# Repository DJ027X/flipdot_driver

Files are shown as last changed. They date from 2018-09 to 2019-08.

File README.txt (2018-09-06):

######################
A word about the license
######################
In this repo, you'll find the EDA design files for my RISC-V based flipdot display driver.
In the interest of preventing an entity from profiting off of my work or its derivitives without my permission, everything in this repo is released under the Creative Commons license BY-NC-SA.
Feel free to modify and redistribute my work (with attribution to me, and under the same BY-NC-SA license), just don't use the work for profit.
Please contact me if you would like to request exemption from the terms of the license.

######################
Project progress
######################
This project is INCOMPLETE and IN-PROGRESS.
At the moment, only the schematic exists; no layout design yet.
The schematic is very near completion, and I'm currently working on finishing touches, and reviewing the design.

######################
Design details/notes
######################
This project is being designed with the open-source KiCAD toolchain. I'm tending toward openness with this project, but my design does use an FT2232D, and my license isn't truly FOSS compliant. More FOSS friendly versions may come up in the future.
My flipdot display driver is intended for use with a Luminator MAX 3000 flipdot display.
My board will mount onto the back of the flipdot display, and connect to it via a board-to-board connector (samtec part SSQ-132-01-G-Q at the moment).
Each dot on the Luminator MAX 3000 is matrixed in such a way that lends itself to be driven by what is essentially an H-bridge. (diodes in the display circuitry complicate things a tad, which is why it's not exactly an H-bridge driver, but pretty close)
My driver uses power MOSFETs arranged in an H-bridge-like topology to drive current in short (on the order of millisecond) pulses in one direction or another through the coil of each dot to flip it on (bright side visable) or off (black side visible), depending on the cirection of the current
There is 1/2 of this H-bridge-like circuit (quarter bridge?) driving each row and column on the display, effectively allowing the driver to multiplex the dots.
The quarter-bridge driver circuitry is controlled by data stored in 2 (extendable) shift registers, one for the rows and one for the columns.
Pulsing an output enable signal on the shift registers drives the selected quarter-bridge circuits (based on the output from the shift register) for the duration of the pulse.
If one wishes to extend their display with yet another (actually, an arbitrary number of) Luminator MAX 3000 board, I've added a connector that will be used (when I get around to designing the second board) to extend the shift registers to the additional board, which will house it's own section of the shift register and dedicated quarter-bridge driver circuitry.
The brain of the operation is the FE310-G000, a VERY new RISC-V based microcontroller released by SiFive.
Along with the uC are the typical auxilary chips: memory and serial to UART/JTAG to program the uC.
The Luminator MAX 3000 also has 1 LED per dot. They are all connected to the same power pins, so they're either all on, or all off.
I intend to control the brightness with PWM.
Under normal use, the board will be supplied with 12V from a power brick. From there, several buck converters will provide the voltages for the shift registers, memory, uC, etc.
There will also be a voltage negater (generating -12V), to provide a potential of 24V for the LEDs.
I'm currently working full time, so progress on this relatively large hobby project has been slow, but I'll have a physical board eventually! (Aiming for 3 months from now (12/27/2018))

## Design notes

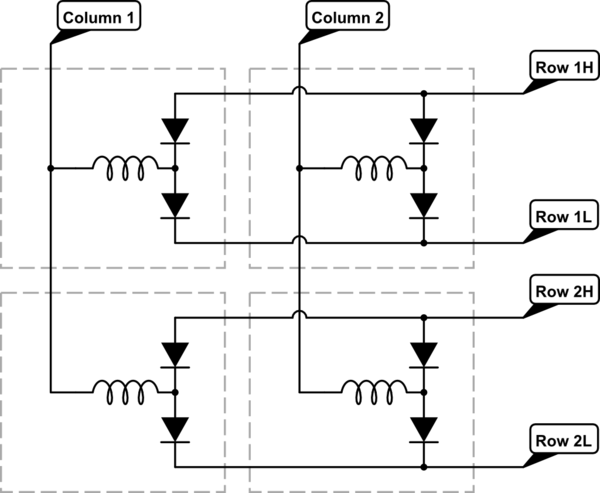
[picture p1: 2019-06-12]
cell_circuit.png

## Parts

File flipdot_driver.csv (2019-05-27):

Reference | Quantity | Value | Footprint | Datasheet | Rating | Capacitance | NP | Resistance
C1 C10 C18 C21 C24 C27 C33 C34 C35 C37 C38 C4 C43 C44 C45 C47 C48 C51 C55 C56 C58 C65 C67 C7 C71 C78 C80 C82 | 28 | CL10B104KO8NNNC | Capacitor_SMD:C_0603_1608Metric | datasheets/CL10B104KO8NNNC.pdf | 16V | 0.1uF
C13 | 1 | NP_470uF
C14 C15 | 2 | ‎ESK476M035AC3AA‎ |  | datasheets/‎KEM_A4004_ESK.pdf | 35V | 47uF
C11 C19 C2 C22 C25 C28 C36 C46 C5 C52 C57 C59 C66 C68 C70 C74 C79 C8 C81 C83 | 20 | CL10B105KA8NNNC | Capacitor_SMD:C_0603_1608Metric | datasheets/CL10B105KA8NNNC.pdf | 25V | 1uF
C12 C20 C23 C26 C29 C3 C39 C49 C53 C6 C69 C84 C9 | 13 | NP_C_0603 | Capacitor_SMD:C_0603_1608Metric |  |  |  | NP
C16 C17 C30 C31 C32 | 5 | ‎CL21A475KLCLQNC‎ | Capacitor_SMD:C_0805_2012Metric | datasheets/‎CL21A475KLCLQNC‎.pdf | 35V | 4.7uF
C40 C41 | 2 | EEE-1VA220SP |  | datasheets/EEE-1VA220SP.pdf | 35V | 22uF
C42 | 1 | 885012206087 | Capacitor_SMD:C_0603_1608Metric | datasheets/885012206087.pdf | 50V | 4.7nF
C50 | 1 | ‎CL10B153KB8SFNC‎ | Capacitor_SMD:C_0603_1608Metric | datasheets/‎CL10B153KB8SFNC‎.pdf | 50V | 15nF
C54 | 1 | 33nF | Capacitor_SMD:C_0603_1608Metric
C60 C62 C75 C77 | 4 | CL21A226MOCLRNC | Capacitor_SMD:C_0805_2012Metric | datasheets/CL21A226MOCLRNC.pdf | 16V | 22uF
C61 C76 | 2 | ‎C0603C470J1GACTU‎ | Capacitor_SMD:C_0603_1608Metric | datasheets/‎C0603C470J1GACTU‎.pdf | 100V | 47pF
C63 C64 C72 C73 | 4 | TMK042CG120JD-W‎ | Capacitor_SMD:C_01005_0402Metric | datasheets/TMK042CG120JD-W‎.pdf | 25V | 12pF
D1 D10 D11 D12 D13 D14 D15 D16 D17 D18 D19 D2 D20 D21 D22 D23 D24 D25 D26 D27 D28 D29 D3 D30 D31 D32 D4 D5 D6 D7 D8 D9 | 32 | MMBZ5243BLT1G |  |  | 13V
D33 D36 | 2 | DST2080S
D34 | 1 | SMAJ12A | Footprint
D37 | 1 | SMF5.0A | Footprint
D38 D39 | 2 | NP_UCLAMP2501T.TCT | Footprint
D40 | 1 | UCLAMP2501T.TCT | Footprint
D41 | 1 | RSB6.8F2T106
D35 D42 D43 D44 D45 D46 D47 | 7 | LED
J1 | 1 | 10x2_1&3_loaded_2.5mm_0.1in_female_header
J2 | 1 | Barrel_Jack | Connectors:BARREL_JACK
J3 | 1 | Screw_Terminal_01x04
J4 J6 | 2 | Conn_01x03_Male |  | ~
J5 | 1 | Conn_01x08_Male
J7 | 1 | USB-C_Connector
J8 | 1 | NP_Conn_01x06_Male
L1 L3 | 2 | FBMH4532HM681-T
L2 | 1 | 12uH
L4 | 1 | 6.5uH
L5 | 1 | 3.3uH
Q21 Q22 Q23 Q24 Q25 Q26 Q27 Q28 Q29 Q30 Q31 Q32 Q33 Q34 Q35 Q36 Q37 Q38 Q39 Q40 Q61 Q62 Q63 Q64 Q65 Q66 Q67 Q68 Q69 Q70 Q71 Q72 Q73 Q74 Q75 Q76 Q77 Q78 Q79 Q80 Q85 Q86 Q87 Q88 Q90 Q91 Q92 Q93 Q94 Q95 Q96 Q97 | 52 | SSM3K35AMFV |  | datasheets/SSM3K35AMFV.pdf
Q1 Q10 Q11 Q12 Q13 Q14 Q15 Q16 Q17 Q18 Q19 Q2 Q20 Q3 Q4 Q41 Q42 Q43 Q44 Q45 Q46 Q47 Q48 Q49 Q5 Q50 Q51 Q52 Q53 Q54 Q55 Q56 Q57 Q58 Q59 Q6 Q60 Q7 Q8 Q81 Q82 Q83 Q84 Q9 | 44 | DMG6602 | Package_TO_SOT_SMD:TSOT-23-6
Q89 | 1 | DMG6602 | TSOT-23-6
R155 | 1 | 300k | Resistors_SMD:R_0603_HandSoldering
R157 | 1 | 16.2k | Resistors_SMD:R_0603_HandSoldering
R159 | 1 | 200 | Resistors_SMD:R_0603_HandSoldering
R160 | 1 | 143k | Resistors_SMD:R_0603_HandSoldering
R165 R167 | 2 | 47 | Resistors_SMD:R_0603_HandSoldering
R134 R136 R140 R141 R143 R144 R148 R154 R166 R168 R178 R184 R185 R193 R195 R196 R197 | 17 | NP_R_0603 | Resistor_SMD:R_0603_1608Metric |  |  |  |  | NP
R171 | 1 | 1.5k | Resistors_SMD:R_0603_HandSoldering
R173 | 1 | 59k | Resistors_SMD:R_0603_HandSoldering
R172 R175 | 2 | 13k | Resistors_SMD:R_0603_HandSoldering
R169 R177 R181 | 3 | RC0603FR-0747KL | Resistor_SMD:R_0603_1608Metric | datasheets/‎SEI-RMCF_RMCP.pdf |  |  |  | 47k
R156 R164 R179 R192 R194 | 5 | RC0603JR-070RL | Resistor_SMD:R_0603_1608Metric | datasheets/‎PYu-RC_Group_51_RoHS_L_9.pdf |  |  |  | 0
R170 R180 | 2 | 40.2k | Resistors_SMD:R_0603_HandSoldering
R182 | 1 | 100k | Resistors_SMD:R_0603_HandSoldering
R183 | 1 | 32.4k | Resistors_SMD:R_0603_HandSoldering
R163 R186 R187 R188 R189 R190 R191 | 7 | ‎RMCF0603FT470R‎ | Resistor_SMD:R_0603_1608Metric | datasheets/SEI-RMCF_RMCP.pdf |  |  |  | 470
R1 R10 R100 R101 R102 R103 R104 R105 R106 R107 R108 R109 R11 R110 R111 R112 R113 R114 R115 R116 R117 R118 R119 R12 R120 R121 R122 R123 R124 R125 R126 R127 R128 R129 R13 R130 R131 R132 R133 R135 R137 R138 R139 R14 R142 R145 R146 R147 R149 R15 R150 R151 R152 R153 R158 R16 R161 R162 R17 R174 R176 R18 R19 R198 R199 R2 R20 R200 R201 R202 R203 R21 R22 R23 R24 R25 R26 R27 R28 R29 R3 R30 R31 R32 R33 R34 R35 R36 R37 R38 R39 R4 R40 R41 R42 R43 R44 R45 R46 R47 R48 R49 R5 R50 R51 R52 R53 R54 R55 R56 R57 R58 R59 R6 R60 R61 R62 R63 R64 R65 R66 R67 R68 R69 R7 R70 R71 R72 R73 R74 R75 R76 R77 R78 R79 R8 R80 R81 R82 R83 R84 R85 R86 R87 R88 R89 R9 R90 R91 R92 R93 R94 R95 R96 R97 R98 R99 | 157 | CRG0603F4K7 | Resistor_SMD:R_0603_1608Metric | datasheets/PYu-RC_Group_51_RoHS_L_9.pdf |  |  |  | 4.7k
SW1 | 1 | NP_TACTILE_SWITCH | CUSTOM:TACTILE_SWITCH
SW2 | 1 | TACTILE_SWITCH | CUSTOM:TACTILE_SWITCH
TP1 TP10 TP11 TP12 TP13 TP14 TP15 TP16 TP17 TP18 TP19 TP20 TP21 TP22 TP23 TP24 TP25 TP26 TP27 TP28 TP29 TP3 TP30 TP31 TP32 TP33 TP34 TP35 TP36 TP37 TP38 TP4 TP40 TP42 TP5 TP6 TP7 TP8 TP9 | 39 | TestPoint |  | ~
TP2 TP39 TP41 | 3 | TEST
U1 U10 U11 U14 U19 U2 U21 U3 U4 U5 U6 | 11 | 74HC595
U12 | 1 | TPS61175
U13 | 1 | FE310-G000
U16 | 1 | FT2232D | Housings_QFP:LQFP-48_7x7mm_Pitch0.5mm
U17 | 1 | IS25LP128-JBLE | Housings_SOIC:SOIC-8_3.9x4.9mm_Pitch1.27mm
U15 U18 | 2 | AP65111A
U20 U22 U7 U8 U9 | 5 | CM1293A-04SO |  | datasheets/CM1293A-04SO-D.PDF
Y1 | 1 | 16MHz
Y2 | 1 | 6MHz

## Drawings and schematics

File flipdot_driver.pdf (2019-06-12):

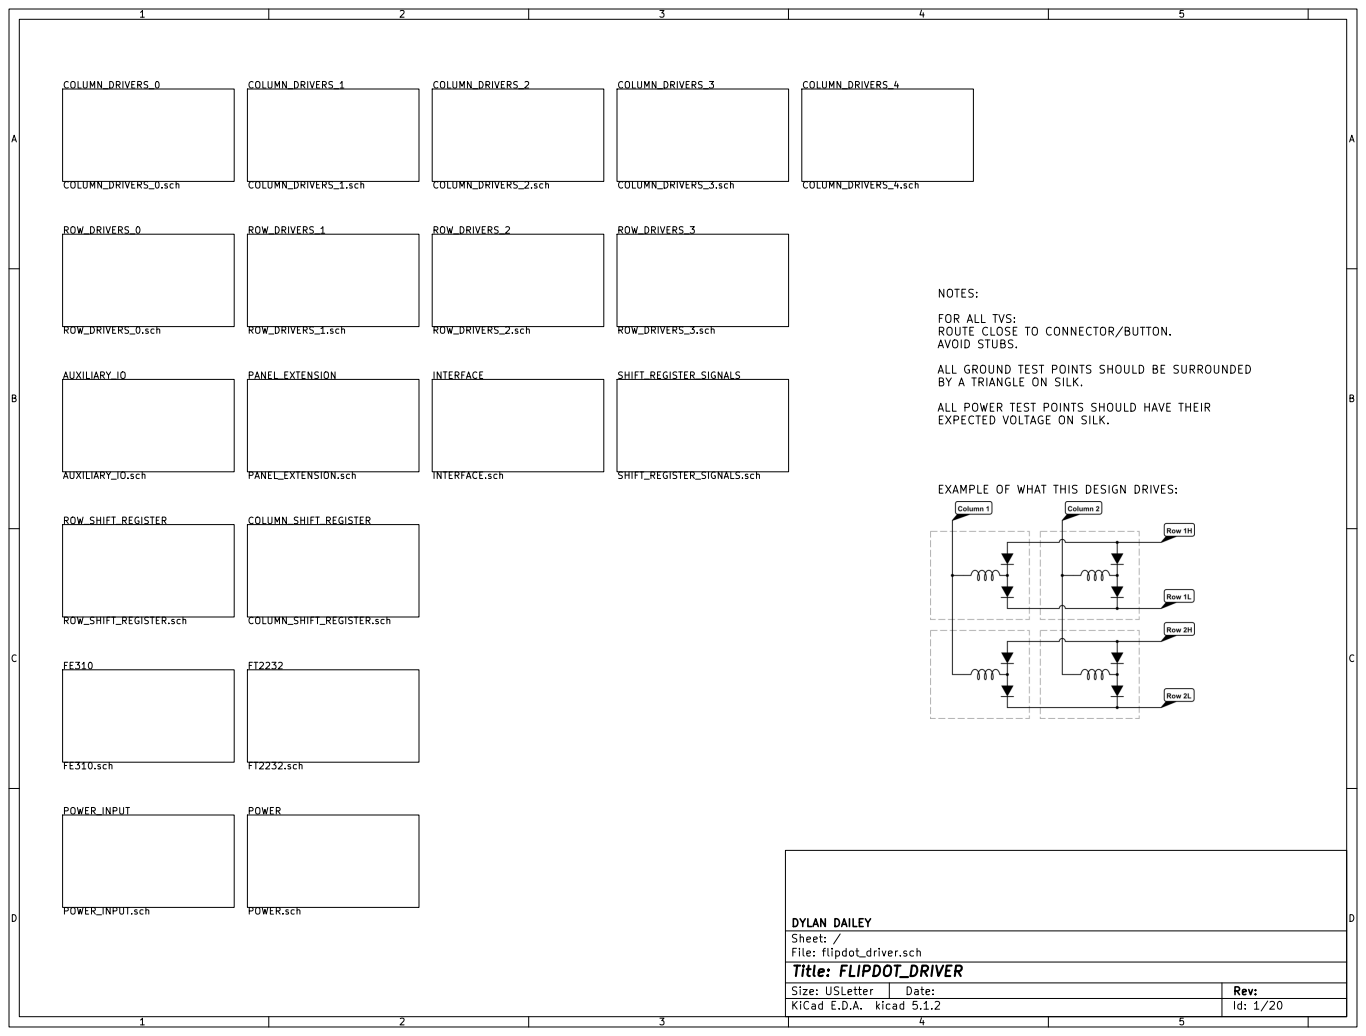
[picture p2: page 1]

FOR ALL TVS:
ROUTE CLOSE TO CONNECTOR/BUTTON.
AVOID STUBS.

ALL GROUND TEST POINTS SHOULD BE SURROUNDED
BY A TRIANGLE ON SILK.

ALL POWER TEST POINTS SHOULD HAVE THEIR
EXPECTED VOLTAGE ON SILK.

EXAMPLE OF WHAT THIS DESIGN DRIVES:

File: flipdot_driver.sch Sheet: / DYLAN DAILEY

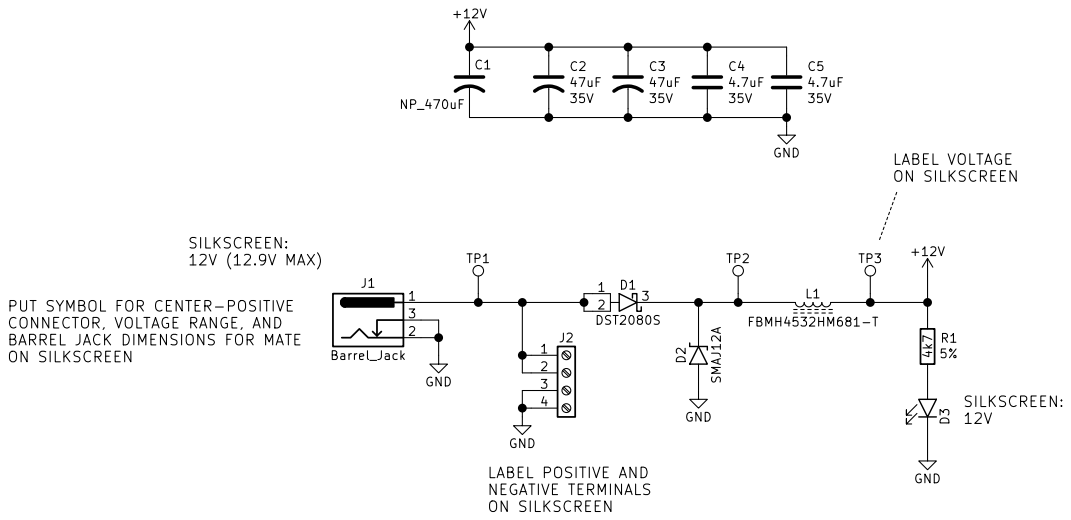
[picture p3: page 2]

J1 Barrel_Jack PUT SYMBOL FOR CENTER-POSITIVE

CONNECTOR, VOLTAGE RANGE, AND
BARREL JACK DIMENSIONS FOR MATE
ON SILKSCREEN

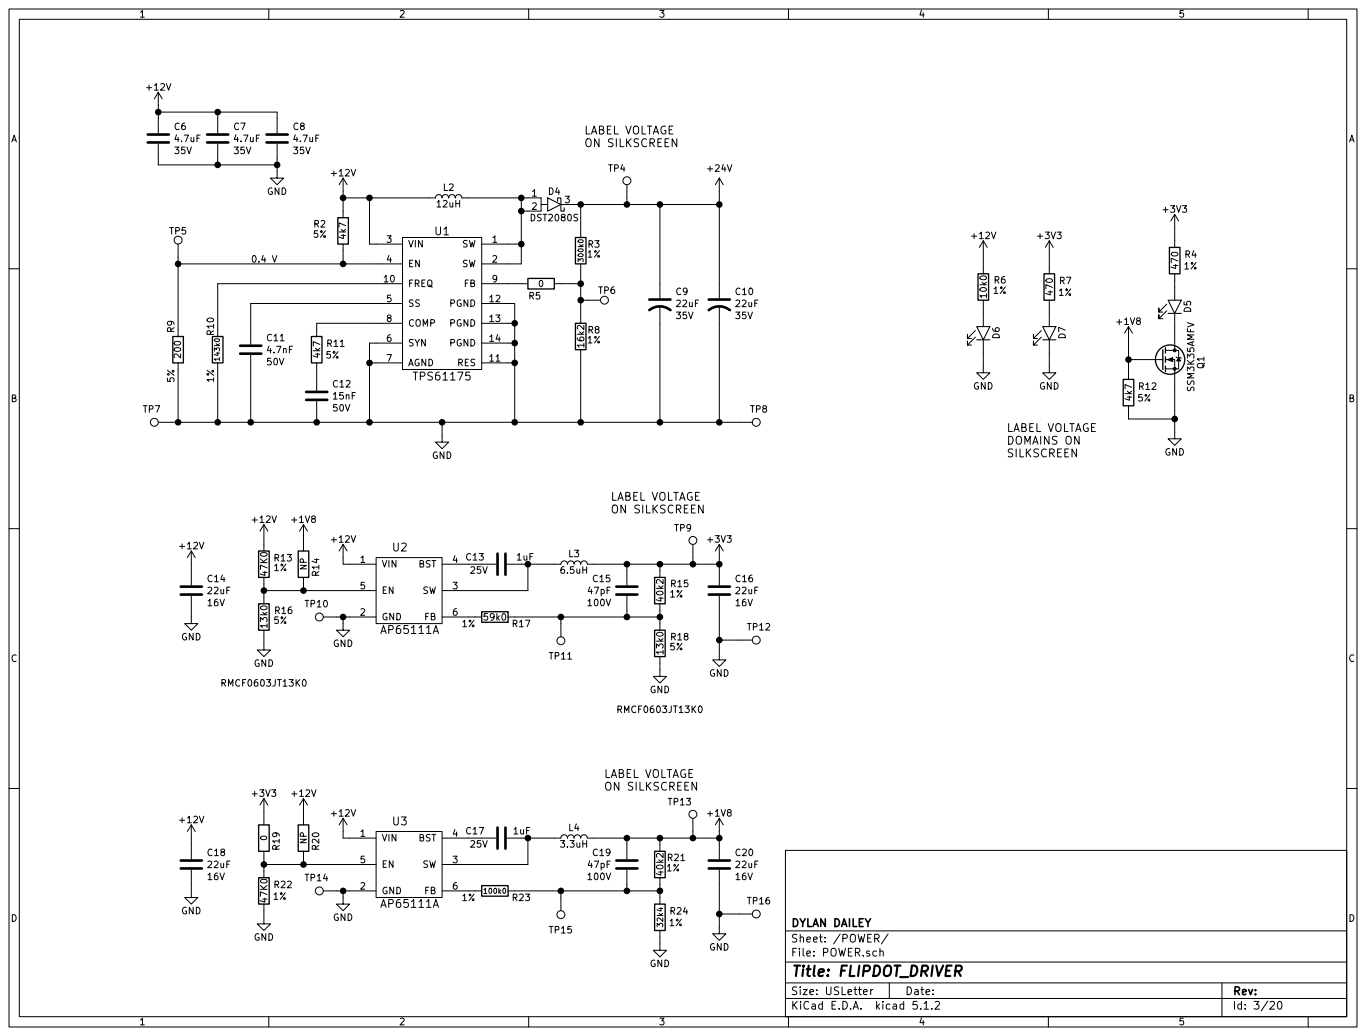
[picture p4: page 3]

File: POWER.sch Sheet: /POWER/ DYLAN DAILEY

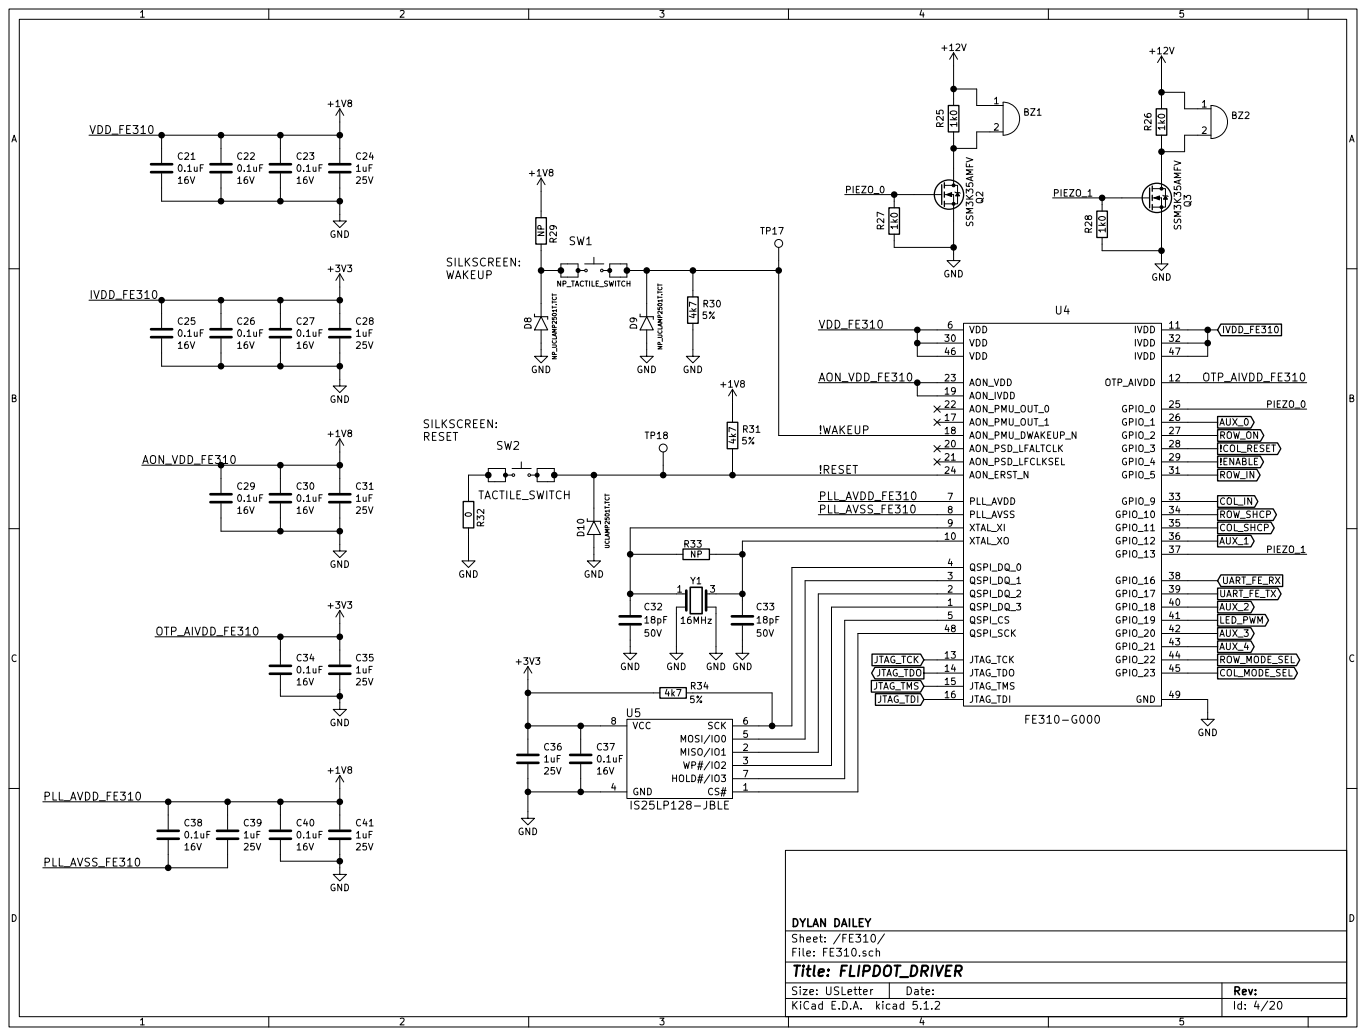
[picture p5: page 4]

File: FE310.sch Sheet: /FE310/ DYLAN DAILEY

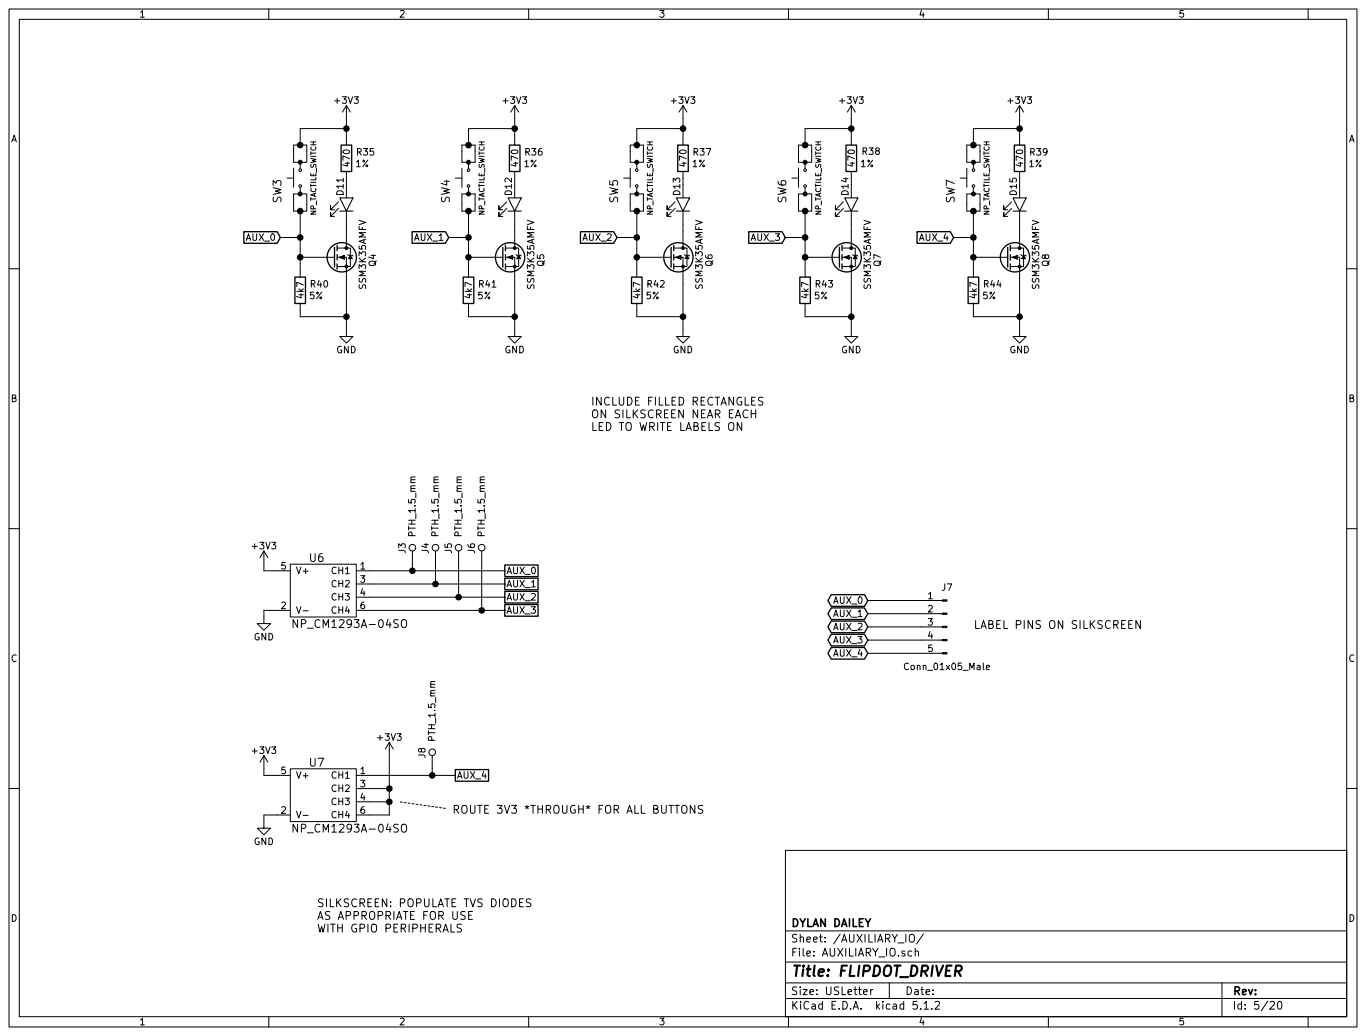
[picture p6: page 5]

INCLUDE FILLED RECTANGLES
ON SILKSCREEN NEAR EACH
LED TO WRITE LABELS ON

LABEL PINS ON SILKSCREEN J3 PTH_1.5_mm J4 PTH_1.5_mm J5 PTH_1.5_mm J6 PTH_1.5_mm

ROUTE 3V3 *THROUGH* FOR ALL BUTTONS

Sheet: /AUXILIARY_IO/ DYLAN DAILEY SILKSCREEN: POPULATE TVS DIODES
AS APPROPRIATE FOR USE
WITH GPIO PERIPHERALS

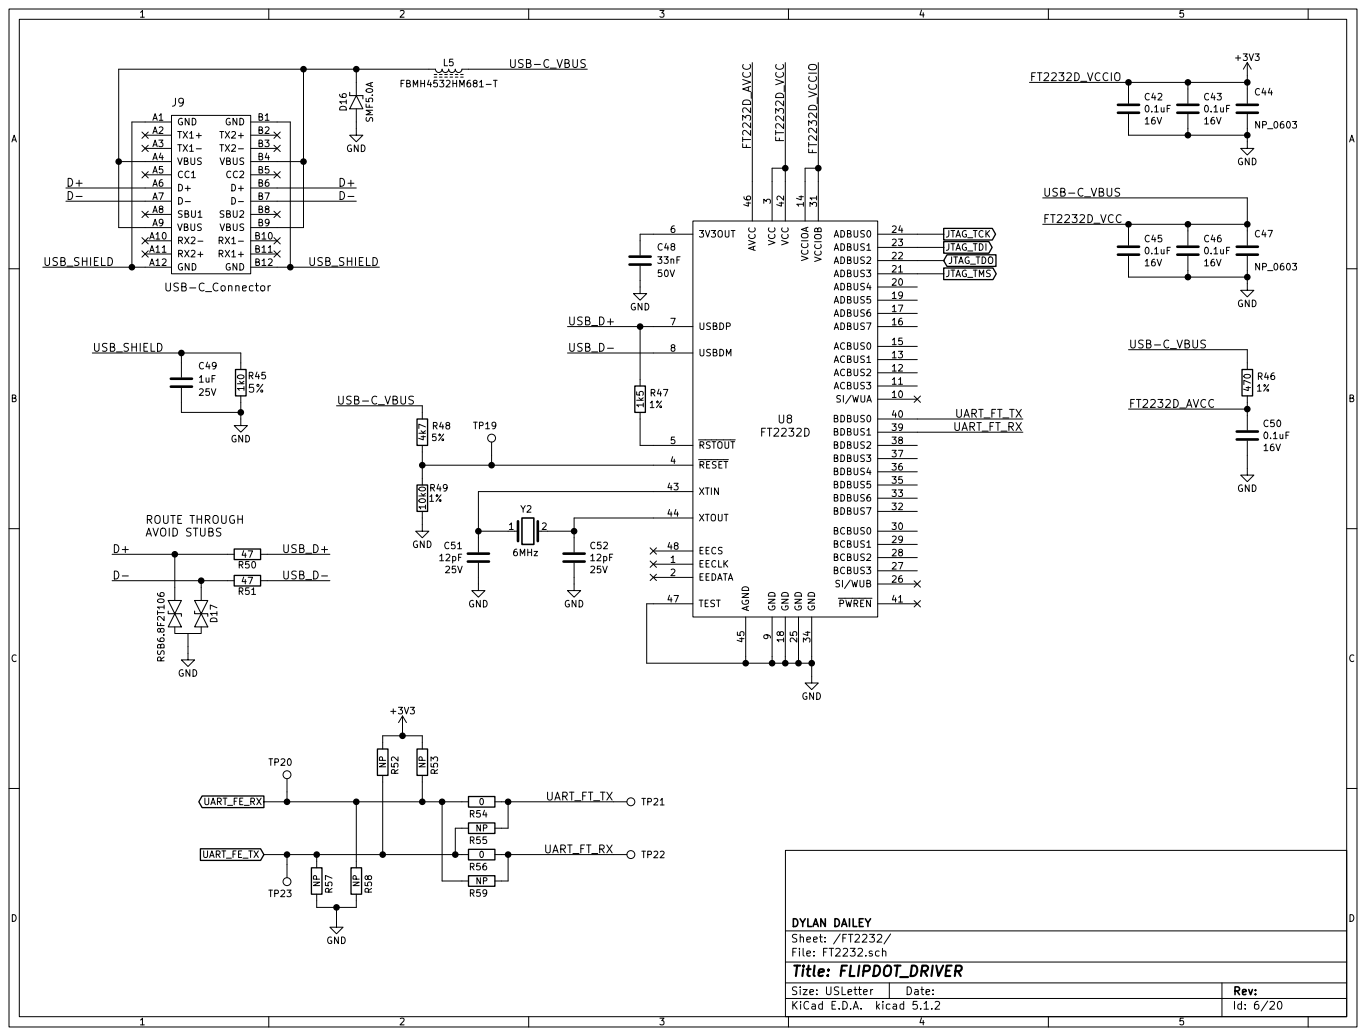
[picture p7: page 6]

3 BCBUS0 30 VCCIOB 31 BDBUS7 32 BDBUS6 33 GND 34 BDBUS5 35 BDBUS4 36 BDBUS3 37 BDBUS2 38 BDBUS1 39 RESET 4 BDBUS0 40 PWREN 41 VCC 42 XTIN 43 XTOUT 44 AGND 45 AVCC 46 TEST 47 EECS 48 RSTOUT 5

File: FT2232.sch Sheet: /FT2232/ DYLAN DAILEY

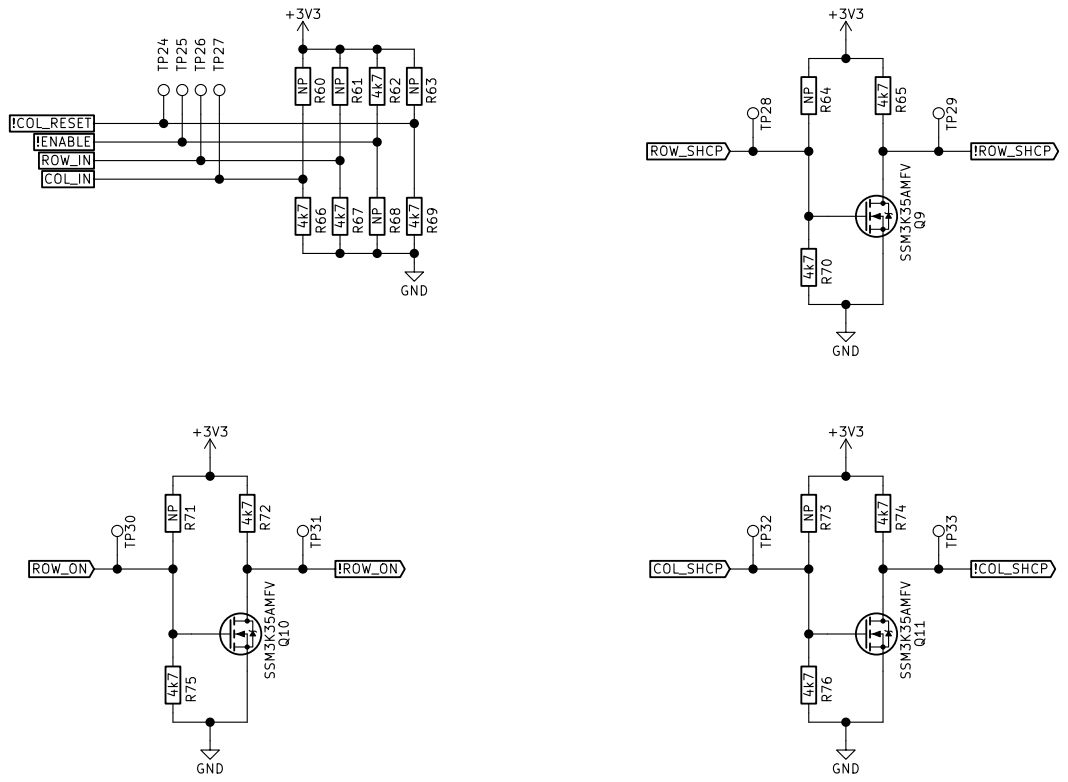
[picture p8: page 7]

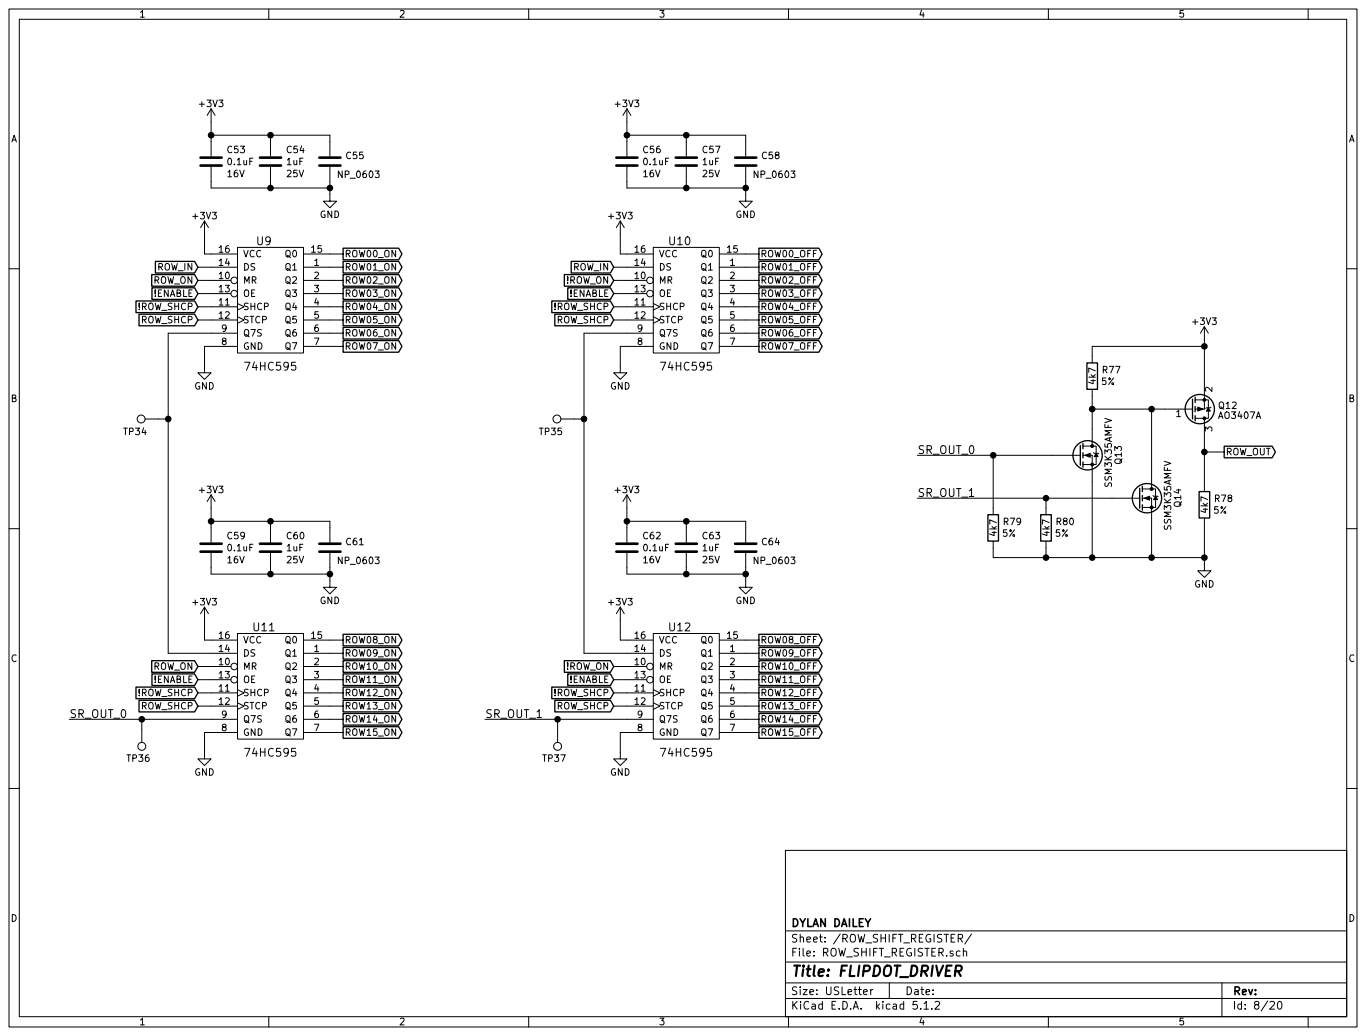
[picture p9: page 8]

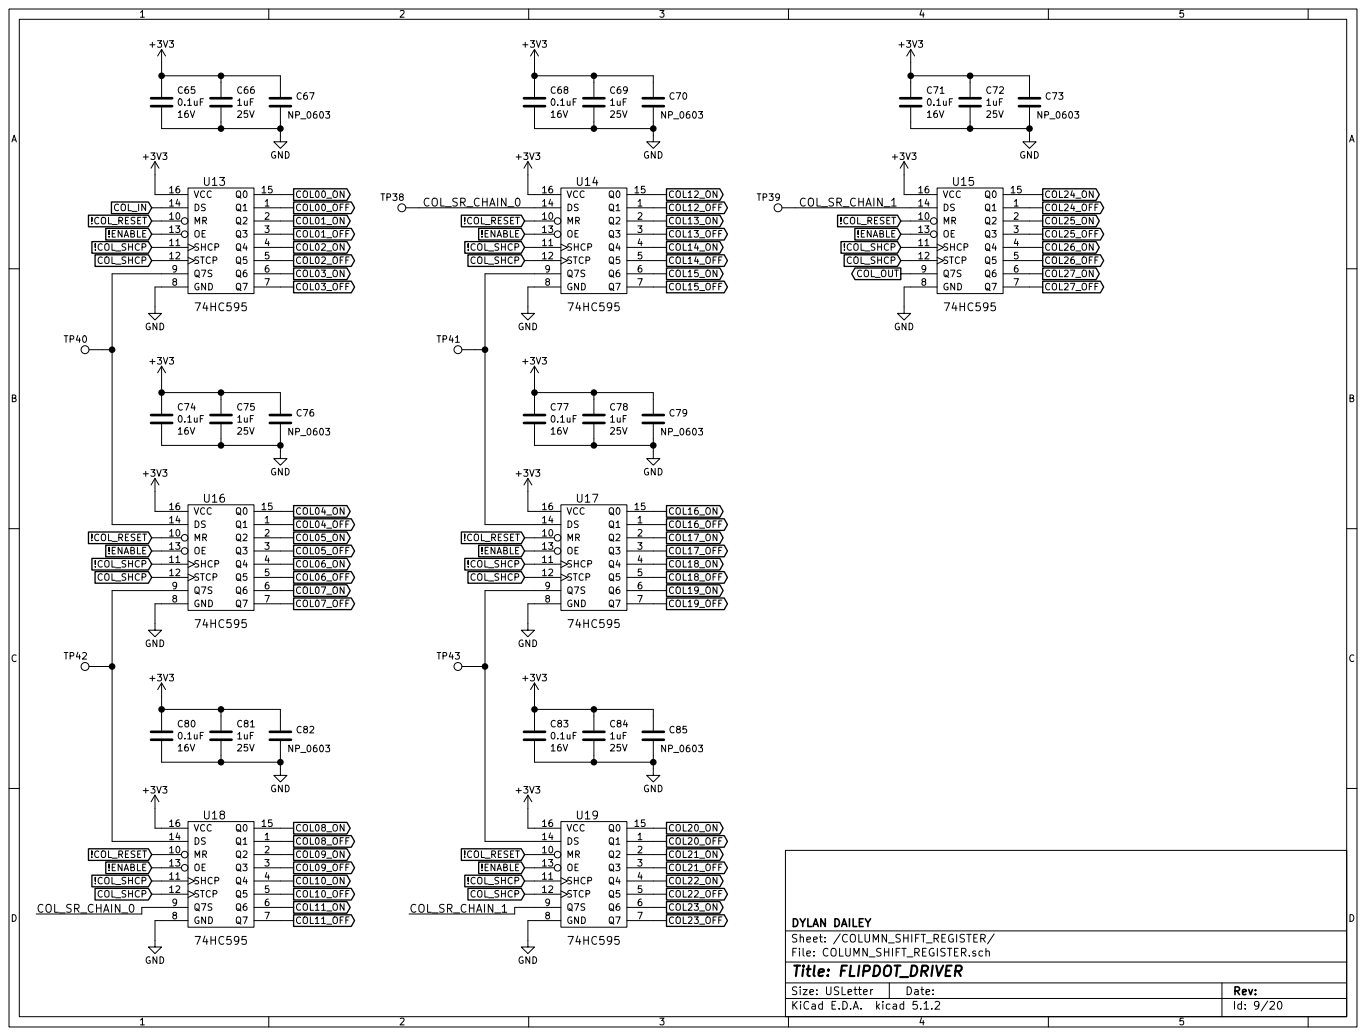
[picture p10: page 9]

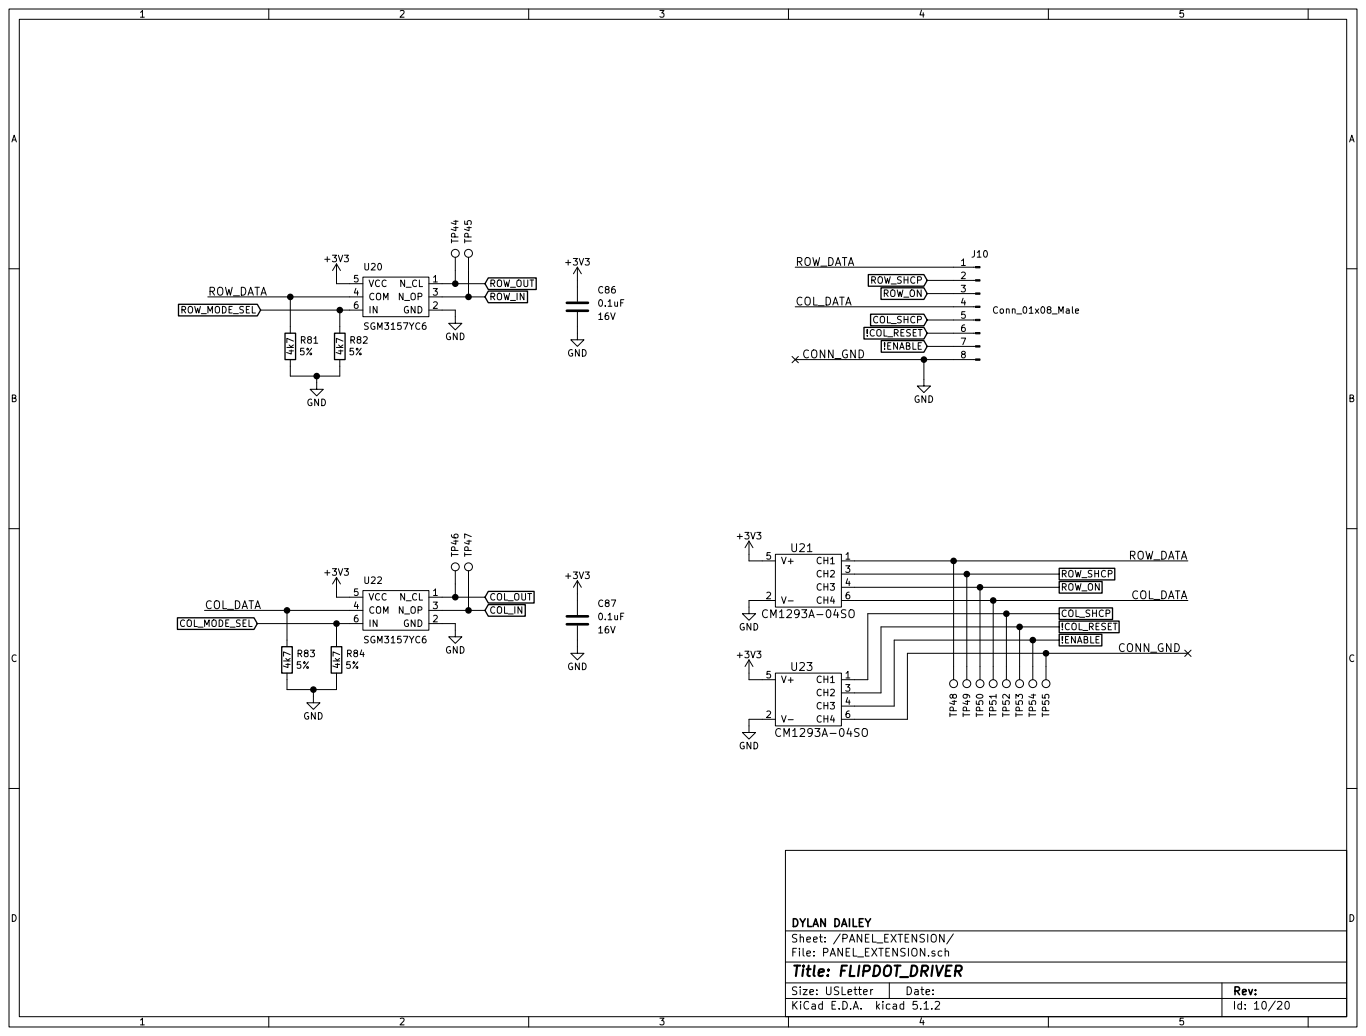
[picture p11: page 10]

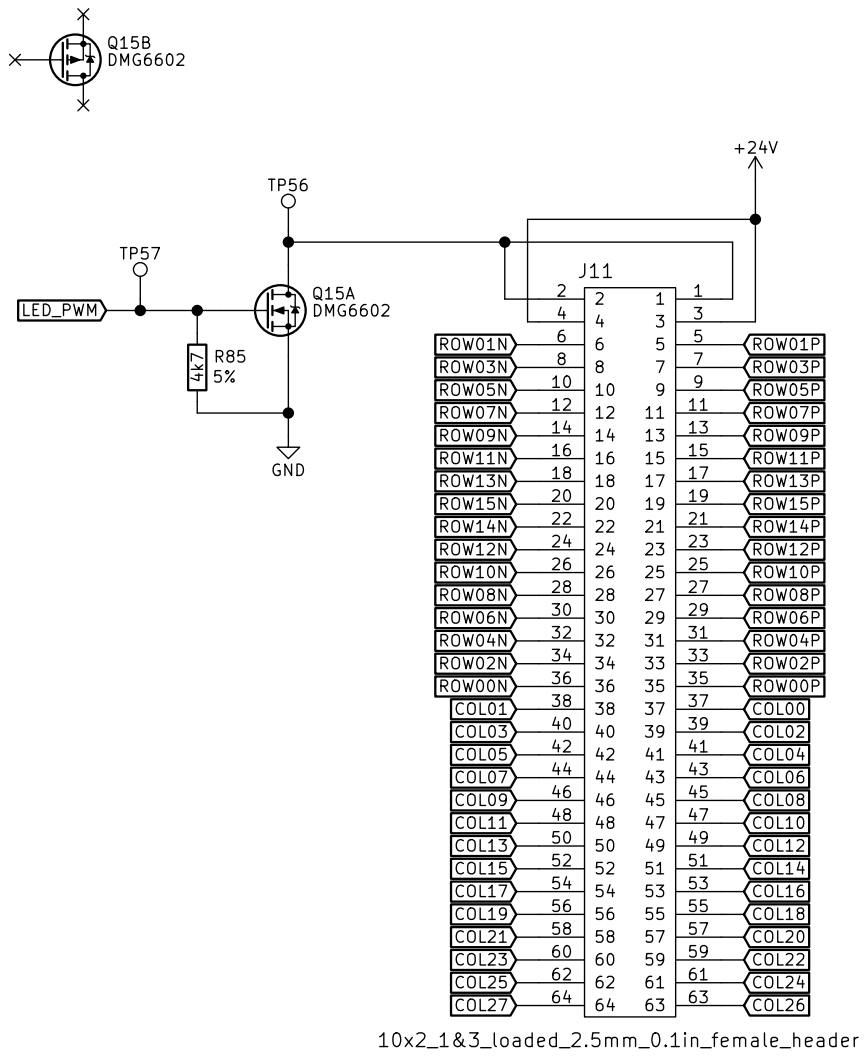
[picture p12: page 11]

File: INTERFACE.sch Sheet: /INTERFACE/ DYLAN DAILEY

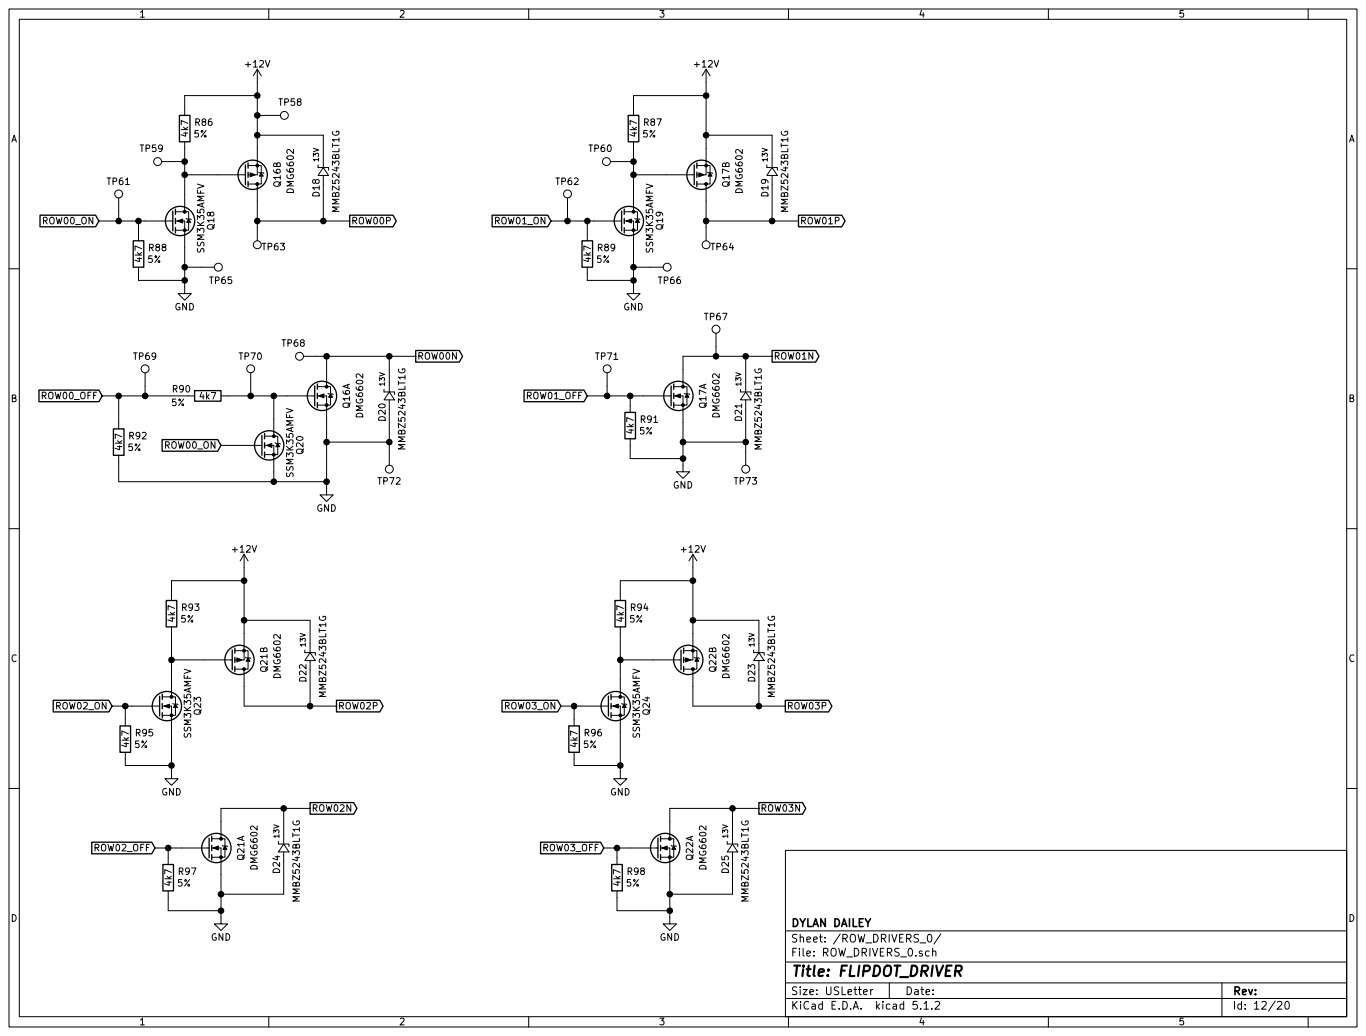
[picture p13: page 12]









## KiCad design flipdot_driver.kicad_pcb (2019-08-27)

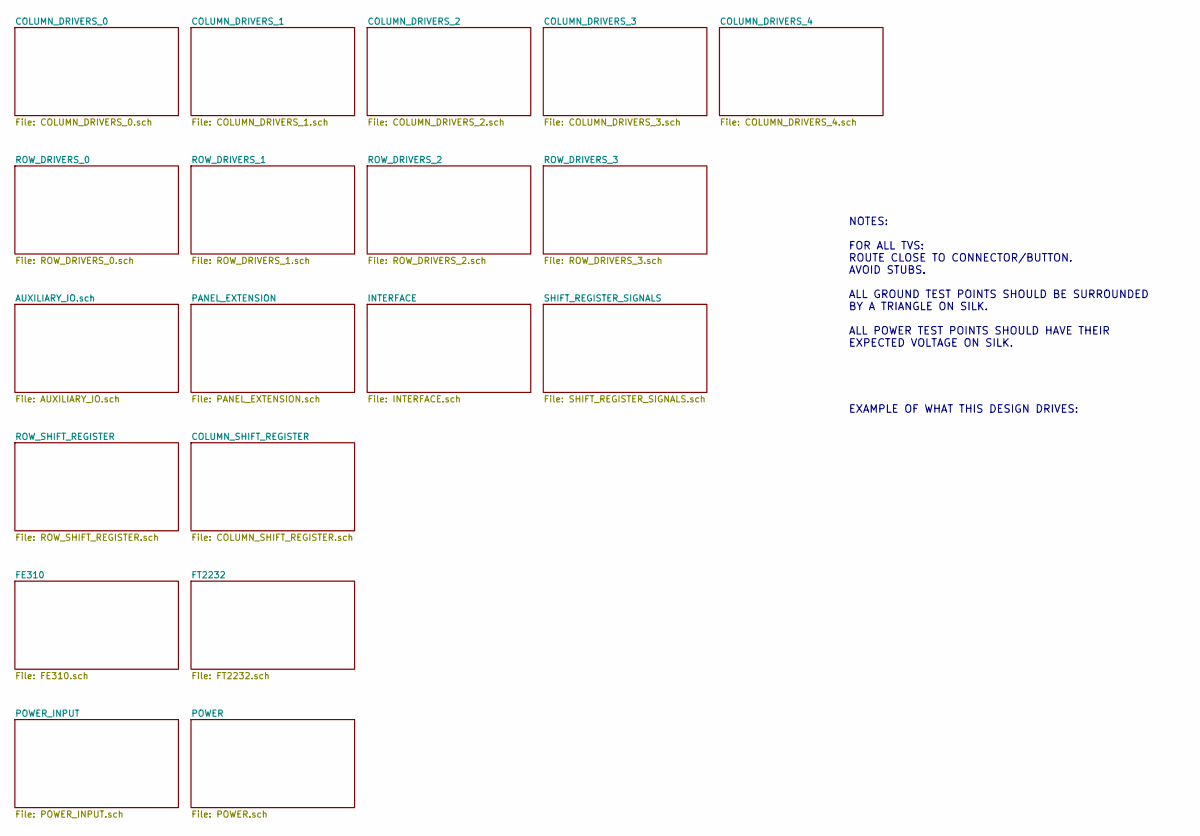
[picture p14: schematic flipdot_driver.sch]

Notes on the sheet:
NOTES: FOR ALL TVS: ROUTE CLOSE TO CONNECTOR/BUTTON. AVOID STUBS. ALL GROUND TEST POINTS SHOULD BE SURROUNDED BY A TRIANGLE ON SILK. ALL POWER TEST POINTS SHOULD HAVE THEIR EXPECTED VOLTAGE ON SILK.
EXAMPLE OF WHAT THIS DESIGN DRIVES:

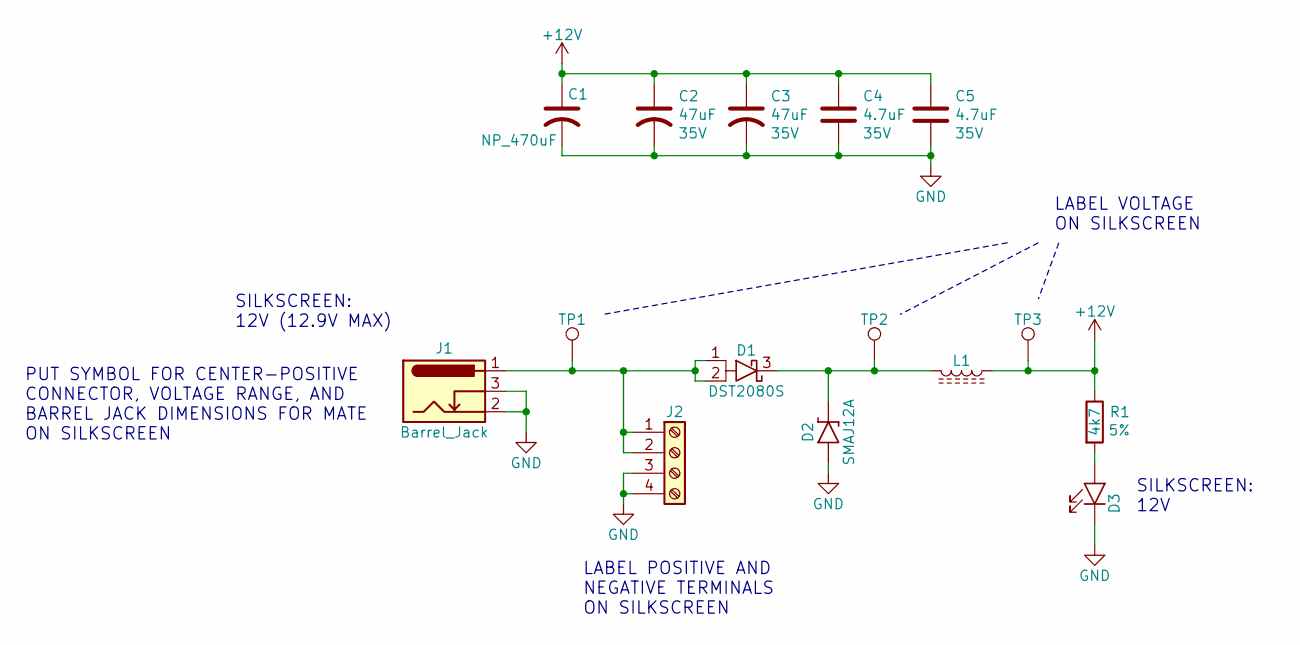
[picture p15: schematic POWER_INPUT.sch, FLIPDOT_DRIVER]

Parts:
C1: NP_470uF
C2, C3: ‎ESK476M035AC3AA‎; Rating 35V
C4, C5: ‎CL21A475KLCLQNC‎; C_0805_2012Metric; Rating 35V
D1: DST2080S; TO-277B
D2: SMAJ12A; D_SMA
D3: LED_GENERIC_0805; D_0805_2012Metric
J1: Barrel_Jack; BarrelJack_Wuerth_6941xx301002
J2: Screw_Terminal_01x04; TERMINAL_BLOCK_5mm_1x4
L1: BLM31SN500SZ1L; L_1206_3216Metric
R1: CRG0603F4K7; R_0603_1608Metric; TOLERANCE 5%
TP1, TP2, TP3: TestPoint; TestPoint_THTPad_D1.0mm_Drill0.5mm

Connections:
+12V: C1.1, C2.1, C3.1, C4.1, C5.1, L1.1, R1.1, TP3.1; also elsewhere on the board
GND: C1.2, C2.2, C3.2, C4.2, C5.2, D2.2 (A), D3.1 (K), J1.2, J1.3, J2.3, J2.4; also elsewhere on the board
unnamed: D1.1 (A1), D1.2 (A2), J1.1, J2.1, J2.2, TP1.1
unnamed: D1.3 (K), D2.1 (K), L1.2, TP2.1
unnamed: D3.2 (A), R1.2

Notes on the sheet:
PUT SYMBOL FOR CENTER-POSITIVE CONNECTOR, VOLTAGE RANGE, AND BARREL JACK DIMENSIONS FOR MATE ON SILKSCREEN
LABEL POSITIVE AND NEGATIVE TERMINALS ON SILKSCREEN
SILKSCREEN: 12V (12.9V MAX)
SILKSCREEN: 12V
LABEL VOLTAGE ON SILKSCREEN

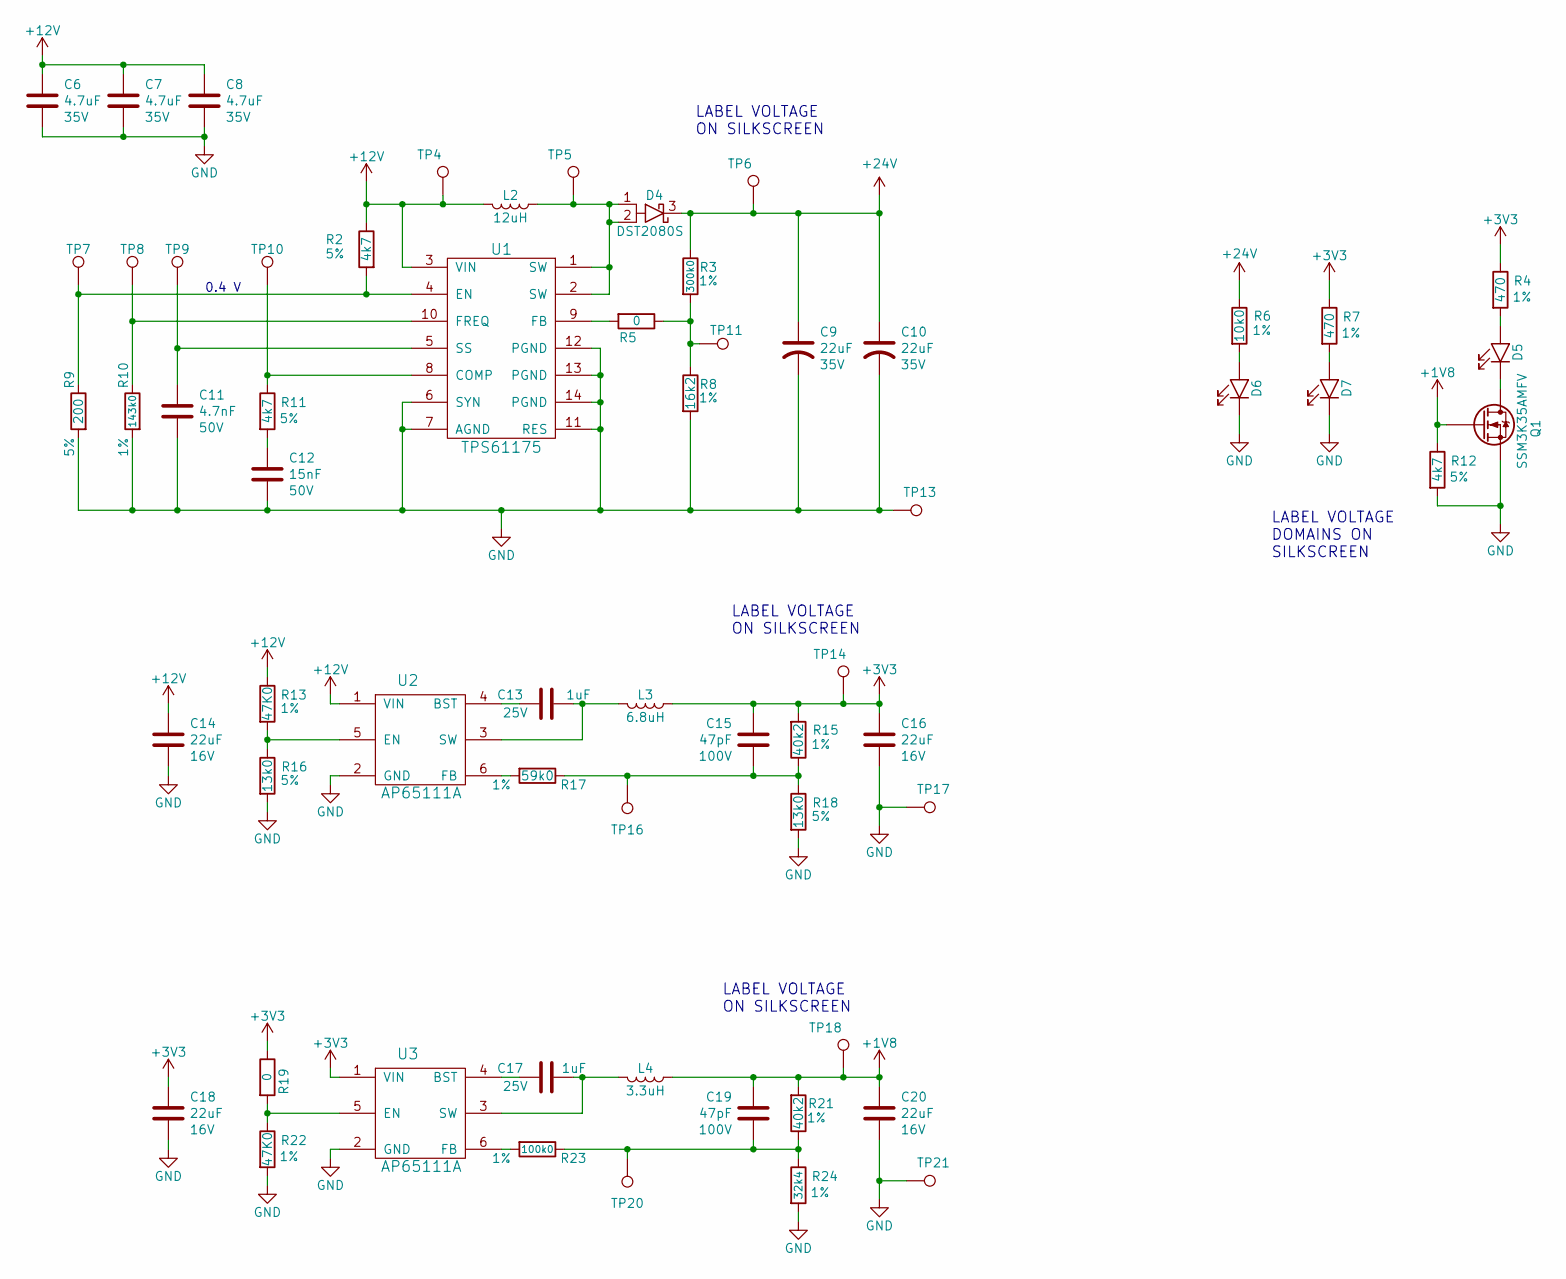
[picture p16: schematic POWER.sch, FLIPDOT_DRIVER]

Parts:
C6, C7, C8: ‎CL21A475KLCLQNC‎; C_0805_2012Metric; Rating 35V
C9, C10: EEE-1VA220SP; Rating 35V
C11: 885012206087; C_0603_1608Metric; Rating 50V
C12: ‎CL10B153KB8SFNC‎; C_0603_1608Metric; Rating 50V
C13, C17: CL10B105KA8NNNC; C_0603_1608Metric; Rating 25V
C14, C16, C18, C20: CL21A226MOCLRNC; C_0805_2012Metric; Rating 16V
C15, C19: ‎C0603C470J1GACTU‎; C_0603_1608Metric; Rating 100V
D4: DST2080S; TO-277B
D5, D6, D7: LED_GENERIC_0805; D_0805_2012Metric
L2: #B966AS-120M=P3; 490-14124-1-ND
L3: NRS5020T6R8MMGJ
L4: MAKK2016T3R3M
Q1: SSM3K35AMFV; SOT-723
R2, R11, R12: CRG0603F4K7; R_0603_1608Metric; TOLERANCE 5%
R3: CR0603-FX-3003ELF; R_0603; TOLERANCE 1%
R4, R7: ‎RMCF0603FT470R‎; R_0603_1608Metric; TOLERANCE 1%
R5, R19: RC0603JR-070RL; R_0603_1608Metric
R6: RMCF0603FT10K0; R_0603; TOLERANCE 1%
R8: RMCF0603FT16K2; R_0603; TOLERANCE 1%
R9: AC0603JR-07200RL; R_0603; TOLERANCE 5%
R10: ERJ-3EKF1433V; R_0603; TOLERANCE 1%
R13, R22: RC0603FR-0747KL; R_0603_1608Metric; TOLERANCE 1%
R15, R21: RMCF0603FT40K2; R_0603; TOLERANCE 1%
R16, R18: RMCF0603JT13K0; R_0603; TOLERANCE 5%
R17: RMCF0603FT59K0; R_0603; TOLERANCE 1%
R23: RMCF0603FG100K; R_0603; TOLERANCE 1%
R24: CR0603-FX-3242ELF; R_0603_1608Metric; TOLERANCE 1%
TP4, TP5, TP6, TP7, TP8, TP9, TP10, TP11, TP13, TP14, TP16, TP17, TP18, TP20, TP21: TestPoint; TestPoint_THTPad_D1.0mm_Drill0.5mm
U1: TPS61175; HTSSOP-14
U2, U3: AP65111A; TSOT-23-6

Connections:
+1V8: C19.1, C20.1, L4.1, Q1.1 (G), R12.1, R21.1, TP18.1; also elsewhere on the board
+3V3: C15.1, C16.1, C18.1, L3.1, R4.1, R7.1, R15.1, R19.1, TP14.1, U3.1 (VIN); also elsewhere on the board
+12V: C6.1, C7.1, C8.1, C14.1, L2.2, R2.1, R13.1, TP4.1, U1.3 (VIN), U2.1 (VIN); also elsewhere on the board
+24V: C9.1, C10.1, D4.3 (K), R3.1, R6.1, TP6.1; also elsewhere on the board
GND: C6.2, C7.2, C8.2, C9.2, C10.2, C11.2, C12.2, C14.2, C16.2, C18.2, C20.2, D6.1 (K), D7.1 (K), Q1.2 (S), R8.2, R9.2, R10.2, R12.2, R16.2, R18.2, R22.2, R24.2, TP13.1, TP17.1, TP21.1, U1.6 (SYN), U1.7 (AGND), U1.11 (RES), U1.12 (PGND), U1.13 (PGND), U1.14 (PGND), U1.15 (Thermal_Pad), U2.2 (GND), U3.2 (GND); also elsewhere on the board
unnamed: C11.1, TP9.1, U1.5 (SS)
unnamed: C12.1, R11.2
unnamed: C13.1, U2.4 (BST)
unnamed: C13.2, L3.2, U2.3 (SW)
unnamed: C15.2, R15.2, R17.1, R18.1, TP16.1
unnamed: C17.1, U3.4 (BST)
unnamed: C17.2, L4.2, U3.3 (SW)
unnamed: C19.2, R21.2, R23.1, R24.1, TP20.1
unnamed: D4.1 (A1), D4.2 (A2), L2.1, TP5.1, U1.1 (SW), U1.2 (SW)
unnamed: D5.1 (K), Q1.3 (D)
unnamed: D5.2 (A), R4.2
unnamed: D6.2 (A), R6.2
unnamed: D7.2 (A), R7.2
unnamed: R2.2, R9.1, TP7.1, U1.4 (EN)
unnamed: R3.2, R5.1, R8.1, TP11.1
unnamed: R5.2, U1.9 (FB)
unnamed: R10.1, TP8.1, U1.10 (FREQ)
unnamed: R11.1, TP10.1, U1.8 (COMP)
unnamed: R13.2, R16.1, U2.5 (EN)
unnamed: R17.2, U2.6 (FB)
unnamed: R19.2, R22.1, U3.5 (EN)
unnamed: R23.2, U3.6 (FB)

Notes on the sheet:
0.4 V
LABEL VOLTAGE DOMAINS ON SILKSCREEN
LABEL VOLTAGE ON SILKSCREEN

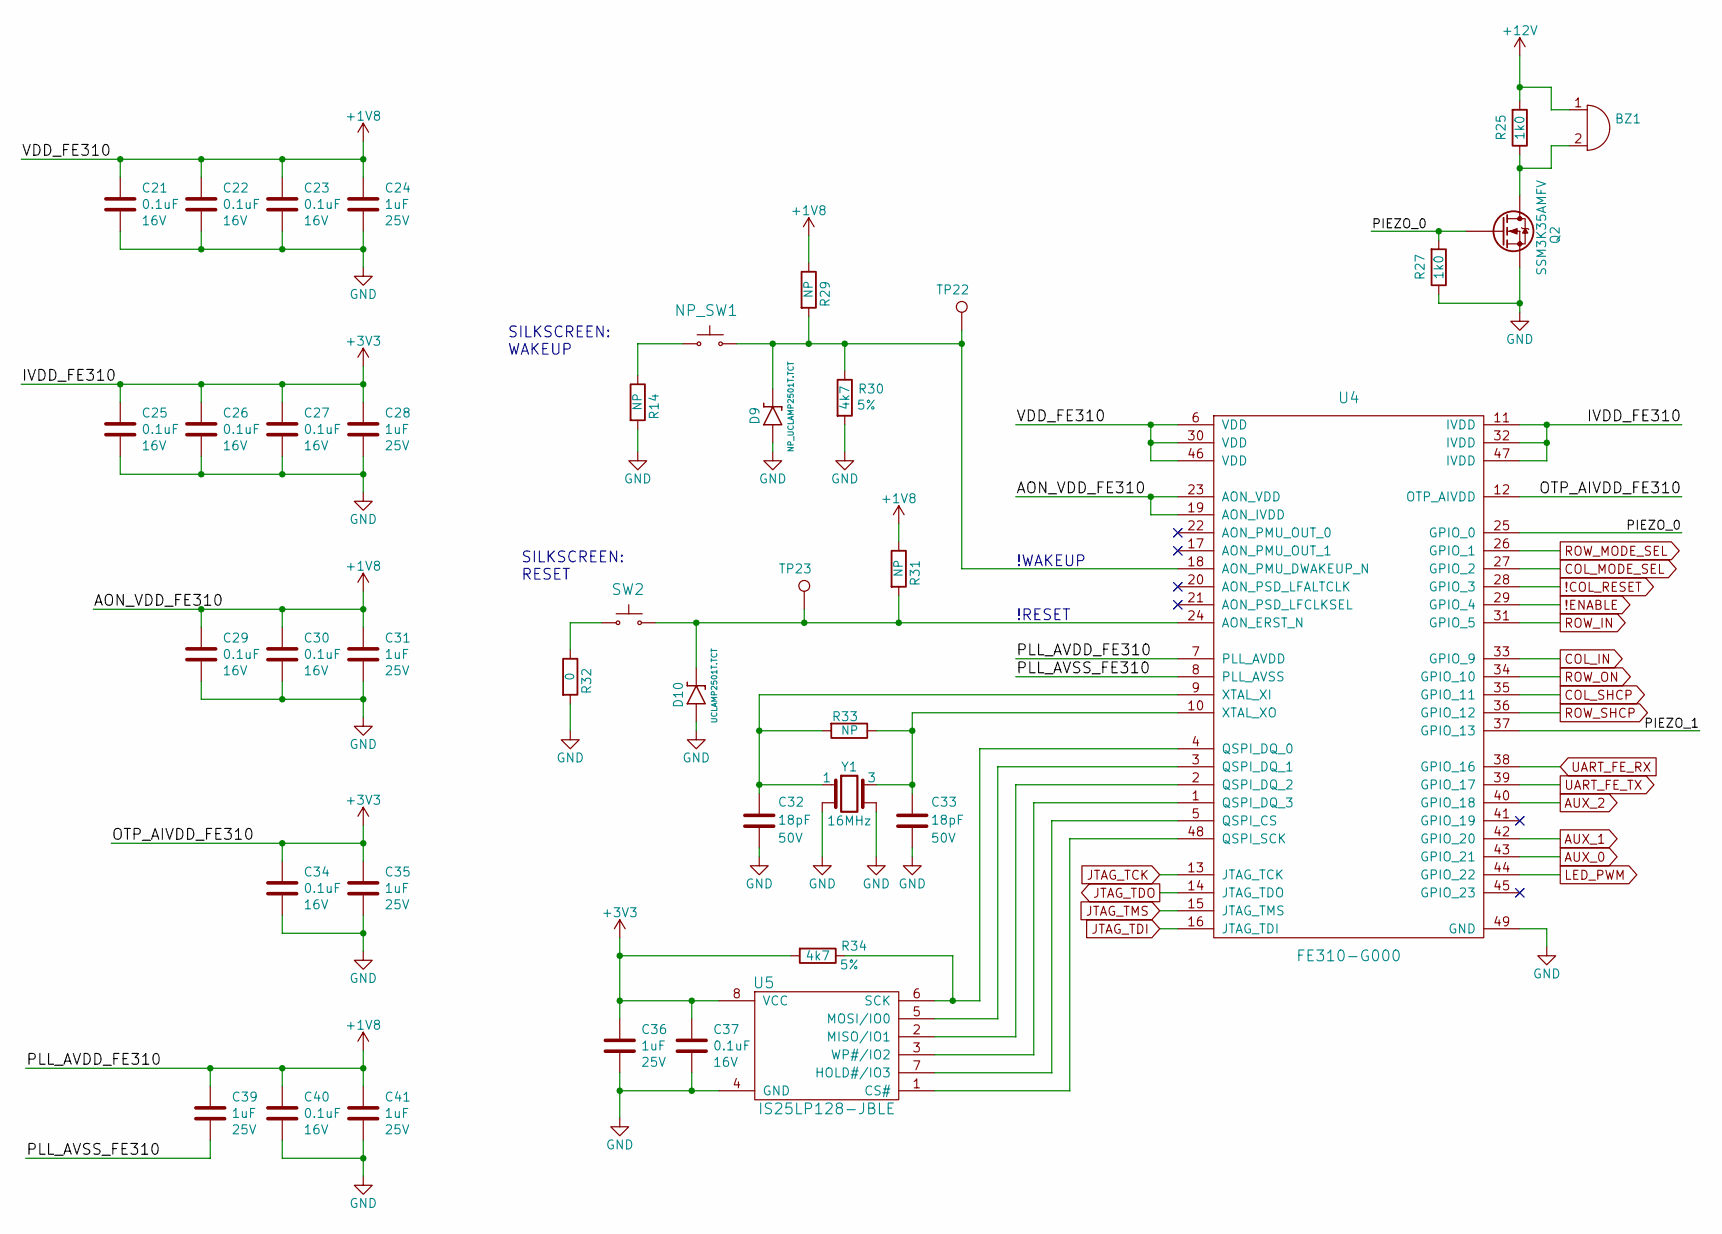
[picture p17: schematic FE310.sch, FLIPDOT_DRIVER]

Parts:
BZ1: PASSIVE_BUZZER; 0.5_IN_BUZZER
C21, C22, C23, C25, C26, C27, C29, C30, C34, C37, C40: CL10B104KO8NNNC; C_0603_1608Metric; Rating 16V
C24, C28, C31, C35, C36, C39, C41: CL10B105KA8NNNC; C_0603_1608Metric; Rating 25V
C32, C33: C0603C180K5RACAUTO; C_0603_1608Metric; Rating 50V
D9: NP_UCLAMP2501T.TCT; SLP1006P2T
D10: UCLAMP2501T.TCT; SLP1006P2T
NP_SW1: NP_TACTILE_SWITCH_SMALL; TACTILE_SWITCH_SMALL
Q2: SSM3K35AMFV; SOT-723
R14, R29, R31, R33: NP_R_0603; R_0603_1608Metric
R25, R27: RC0603JR-071KL; R_0603_1608Metric
R30, R34: CRG0603F4K7; R_0603_1608Metric; TOLERANCE 5%
R32: RC0603JR-070RL; R_0603_1608Metric
SW2: TACTILE_SWITCH_SMALL
TP22, TP23: TestPoint; TestPoint_THTPad_D1.0mm_Drill0.5mm
U4: FE310-G000; QFN-48-1EP_6x6mm_P0.4mm_EP4.3x4.3mm
U5: IS25LP128-JBLE; SOIC-8_3.9x4.9mm_P1.27mm
Y1: 16MHz; 7M-16.000MAAE-T

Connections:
!COL_RESET: U4.28 (GPIO_3); also elsewhere on the board
!ENABLE: U4.29 (GPIO_4); also elsewhere on the board
+1V8: C21.1, C22.1, C23.1, C24.1, C29.1, C30.1, C31.1, C39.1, C40.1, C41.1, R29.1, R31.1, U4.6 (VDD), U4.7 (PLL_AVDD), U4.19 (AON_IVDD), U4.23 (AON_VDD), U4.30 (VDD), U4.46 (VDD); also elsewhere on the board
+3V3: C25.1, C26.1, C27.1, C28.1, C34.1, C35.1, C36.1, C37.1, R34.2, U4.11 (IVDD), U4.12 (OTP_AIVDD), U4.32 (IVDD), U4.47 (IVDD), U5.8 (VCC); also elsewhere on the board
+12V: BZ1.1 (-), R25.1; also elsewhere on the board
/FE310/PIEZO_0: Q2.1 (G), R27.1, U4.25 (GPIO_0)
/FE310/PIEZO_1: U4.37 (GPIO_13)
/FE310/PLL_AVSS_FE310: C39.2, U4.8 (PLL_AVSS)
COL_IN: U4.33 (GPIO_9); also elsewhere on the board
COL_MODE_SEL: U4.27 (GPIO_2); also elsewhere on the board
COL_SHCP: U4.35 (GPIO_11); also elsewhere on the board
GND: C21.2, C22.2, C23.2, C24.2, C25.2, C26.2, C27.2, C28.2, C29.2, C30.2, C31.2, C32.2, C33.2, C34.2, C35.2, C36.2, C37.2, C40.2, C41.2, D9.2 (A), D10.2 (A), Q2.2 (S), R14.2, R27.2, R30.2, R32.2, U4.49 (GND), U5.4 (GND), Y1.2, Y1.4; also elsewhere on the board
JTAG_TCK: U4.13 (JTAG_TCK); also elsewhere on the board
JTAG_TDI: U4.16 (JTAG_TDI); also elsewhere on the board
JTAG_TDO: U4.14 (JTAG_TDO); also elsewhere on the board
JTAG_TMS: U4.15 (JTAG_TMS); also elsewhere on the board
LED_PWM: U4.44 (GPIO_22); also elsewhere on the board
unnamed: BZ1.2 (+), Q2.3 (D), R25.2
unnamed: C32.1, R33.2, U4.9 (XTAL_XI), Y1.1
unnamed: C33.1, R33.1, U4.10 (XTAL_XO), Y1.3
unnamed: D9.1 (K), NP_SW1.2, R29.2, R30.1, TP22.1, U4.18 (AON_PMU_DWAKEUP_N)
unnamed: D10.1 (K), R31.2, SW2.2, TP23.1, U4.24 (AON_ERST_N)
unnamed: NP_SW1.1, R14.1
unnamed: R32.1, SW2.1
unnamed: R34.1, U4.4 (QSPI_DQ_0), U5.6 (SCK)
unnamed: U4.1 (QSPI_DQ_3), U5.3 (WP#/IO2)
unnamed: U4.2 (QSPI_DQ_2), U5.2 (MISO/IO1)
unnamed: U4.3 (QSPI_DQ_1), U5.5 (MOSI/IO0)
unnamed: U4.5 (QSPI_CS), U5.7 (HOLD#/IO3)
unnamed: U4.48 (QSPI_SCK), U5.1 (CS#)
ROW_IN: U4.31 (GPIO_5); also elsewhere on the board
ROW_MODE_SEL: U4.26 (GPIO_1); also elsewhere on the board
ROW_ON: U4.34 (GPIO_10); also elsewhere on the board
ROW_SHCP: U4.36 (GPIO_12); also elsewhere on the board
UART_FE_RX: U4.38 (GPIO_16); also elsewhere on the board
UART_FE_TX: U4.39 (GPIO_17); also elsewhere on the board

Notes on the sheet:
SILKSCREEN: RESET
SILKSCREEN: WAKEUP
!WAKEUP
!RESET

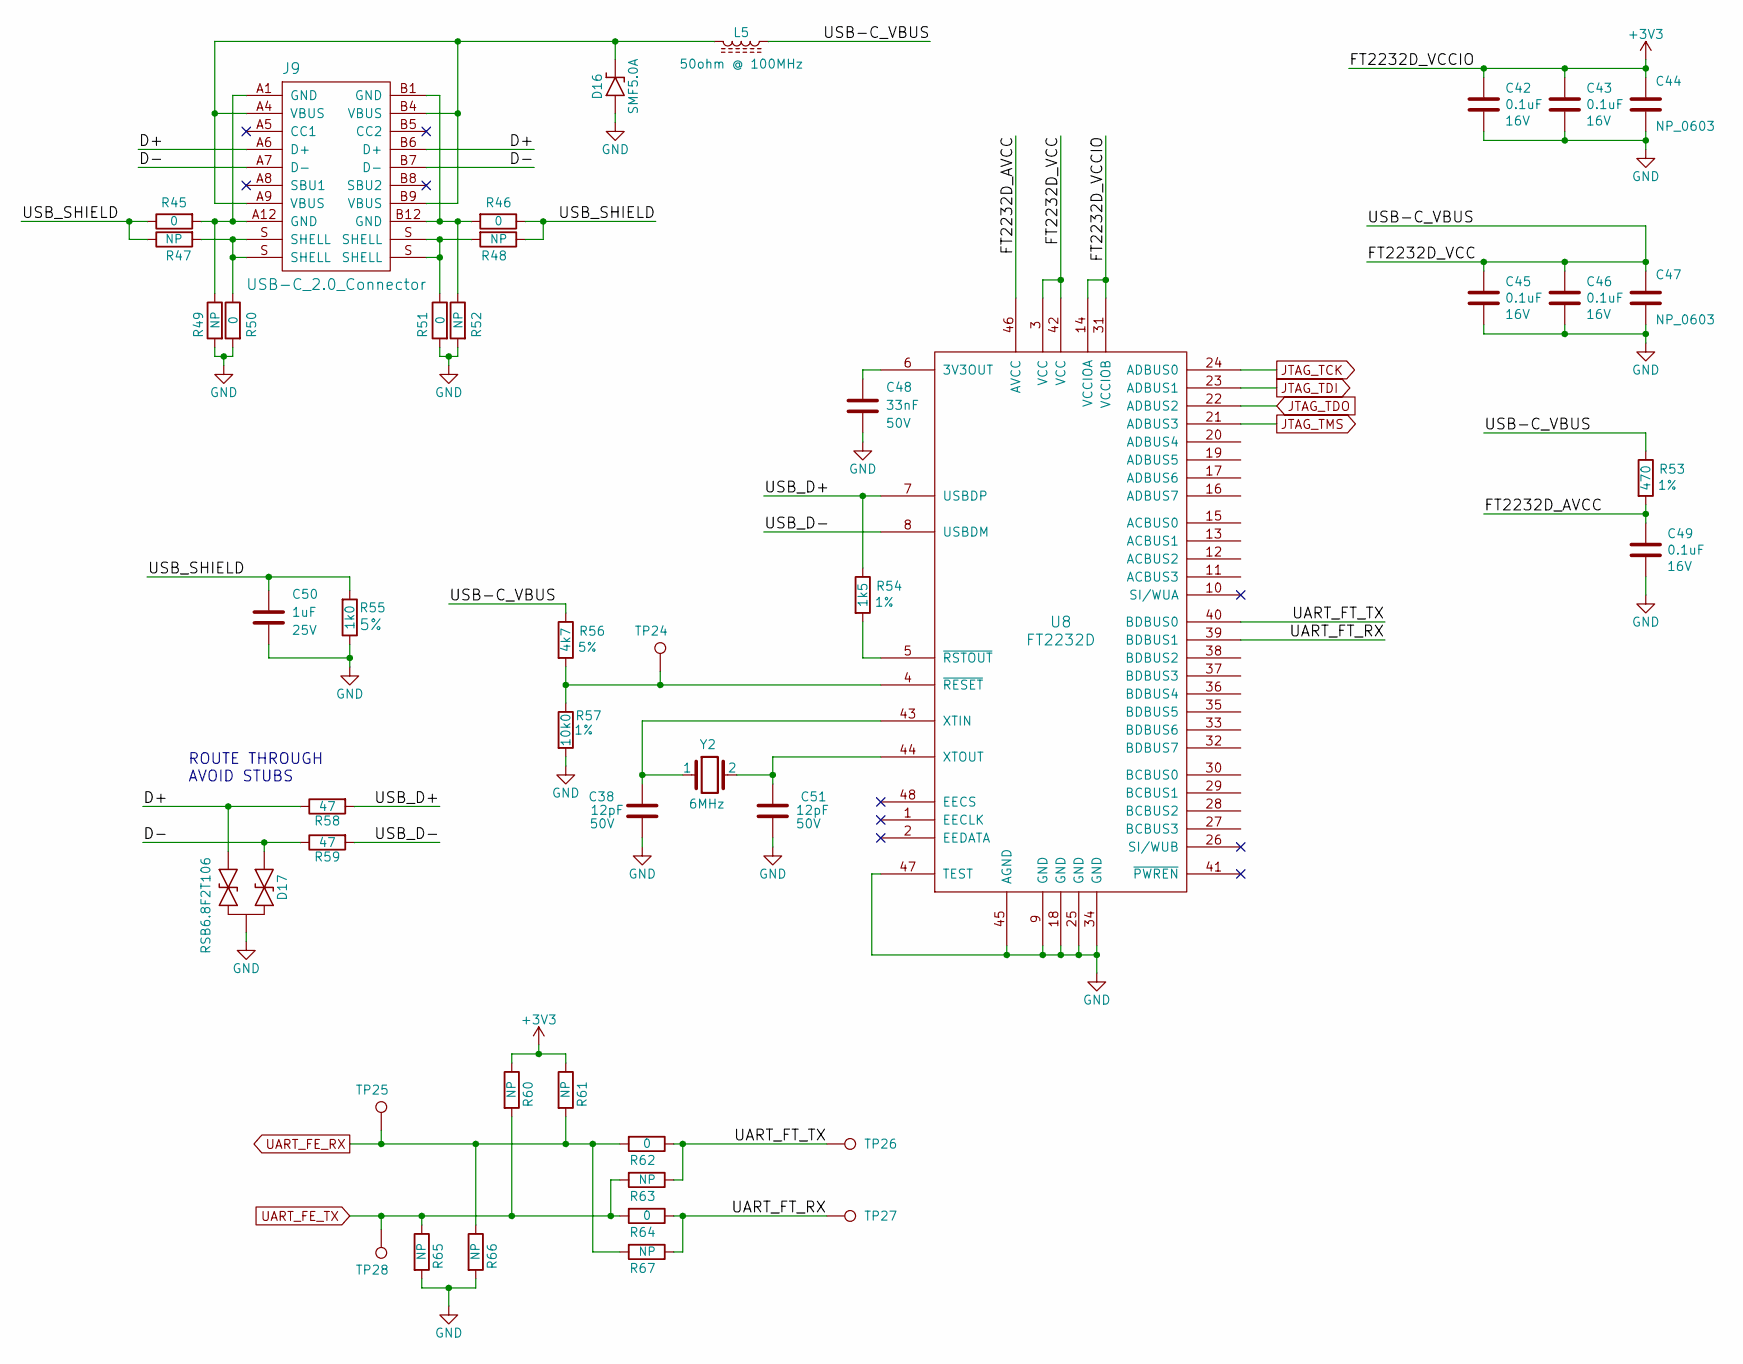
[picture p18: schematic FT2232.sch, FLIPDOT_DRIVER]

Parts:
C38, C51: GRM1555C1H120JA01D; C_0402_1005Metric; RATING 50V; TOLERANCE 5%
C42, C43, C45, C46, C49: CL10B104KO8NNNC; C_0603_1608Metric; Rating 16V
C44, C47: NP_C_0603; C_0603_1608Metric
C48: CL10B333KB8SFNC; C_0603_1608Metric; Rating 50V
C50: CL10B105KA8NNNC; C_0603_1608Metric; Rating 25V
D16: SMF5.0A; SOD-123FL
D17: RSB6.8F2T106; SOT-323_SC-70
J9: USB-C_2.0_Connector; USB4085-GF-A
L5: BLM31SN500SZ1L; L_1206_3216Metric
R45, R46, R50, R51, R62, R64: RC0603JR-070RL; R_0603_1608Metric
R47, R48, R49, R52, R60, R61, R63, R65, R66, R67: NP_R_0603; R_0603_1608Metric
R53: ‎RMCF0603FT470R‎; R_0603_1608Metric; TOLERANCE 1%
R54: RMCF0603FT1K50; R_0603_1608Metric; TOLERANCE 1%
R55: RC0603JR-071KL; R_0603_1608Metric; TOLERANCE 5%
R56: CRG0603F4K7; R_0603_1608Metric; TOLERANCE 5%
R57: RMCF0603FT10K0; R_0603; TOLERANCE 1%
R58, R59: 47; R_0603_1608Metric
TP24, TP25, TP26, TP27, TP28: TestPoint; TestPoint_THTPad_D1.0mm_Drill0.5mm
U8: FT2232D; LQFP-48_7x7mm_P0.5mm
Y2: NX8045GB-6MHZ-STD-CSF-3; NX8045GB

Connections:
+3V3: C42.1, C43.1, C44.1, R60.1, R61.1, U8.14 (VCCIOA), U8.31 (VCCIOB); also elsewhere on the board
/FT2232/D+: D17.1, J9.A6 (D+), J9.B6 (D+), R58.1
/FT2232/D-: D17.2, J9.A7 (D-), J9.B7 (D-), R59.1
/FT2232/FT2232D_AVCC: C49.1, R53.2, U8.46 (AVCC)
/FT2232/FT2232D_VCC: C45.1, C46.1, C47.1, L5.1, R53.1, R56.1, U8.3 (VCC), U8.42 (VCC)
/FT2232/UART_FT_RX: R64.1, R67.1, TP27.1, U8.39 (BDBUS1)
/FT2232/UART_FT_TX: R62.1, R63.1, TP26.1, U8.40 (BDBUS0)
/FT2232/USB_D+: R54.1, R58.2, U8.7 (USBDP)
/FT2232/USB_D-: R59.2, U8.8 (USBDM)
/FT2232/USB_SHIELD: C50.1, R45.1, R46.1, R47.1, R48.1, R55.1
GND: C38.2, C42.2, C43.2, C44.2, C45.2, C46.2, C47.2, C48.2, C49.2, C50.2, C51.2, D16.2 (A), D17.3, R49.2, R50.2, R51.2, R52.2, R55.2, R57.2, R65.2, R66.2, U8.9 (GND), U8.18 (GND), U8.25 (GND), U8.34 (GND), U8.45 (AGND), U8.47 (TEST); also elsewhere on the board
JTAG_TCK: U8.24 (ADBUS0); also elsewhere on the board
JTAG_TDI: U8.23 (ADBUS1); also elsewhere on the board
JTAG_TDO: U8.22 (ADBUS2); also elsewhere on the board
JTAG_TMS: U8.21 (ADBUS3); also elsewhere on the board
unnamed: C38.1, U8.43 (XTIN), Y2.1
unnamed: C48.1, U8.6 (3V3OUT)
unnamed: C51.1, U8.44 (XTOUT), Y2.2
unnamed: D16.1 (K), J9.A4 (VBUS), J9.A9 (VBUS), J9.B4 (VBUS), J9.B9 (VBUS), L5.2
unnamed: J9.A1 (GND), J9.A12 (GND), R45.2, R49.1
unnamed: J9.B1 (GND), J9.B12 (GND), R46.2, R52.1
unnamed: R54.2, U8.5 (~RSTOUT)
unnamed: R56.2, R57.1, TP24.1, U8.4 (~RESET)
UART_FE_RX: R61.2, R62.2, R66.1, R67.2, TP25.1; also elsewhere on the board
UART_FE_TX: R60.2, R63.2, R64.2, R65.1, TP28.1; also elsewhere on the board

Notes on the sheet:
ROUTE THROUGH AVOID STUBS

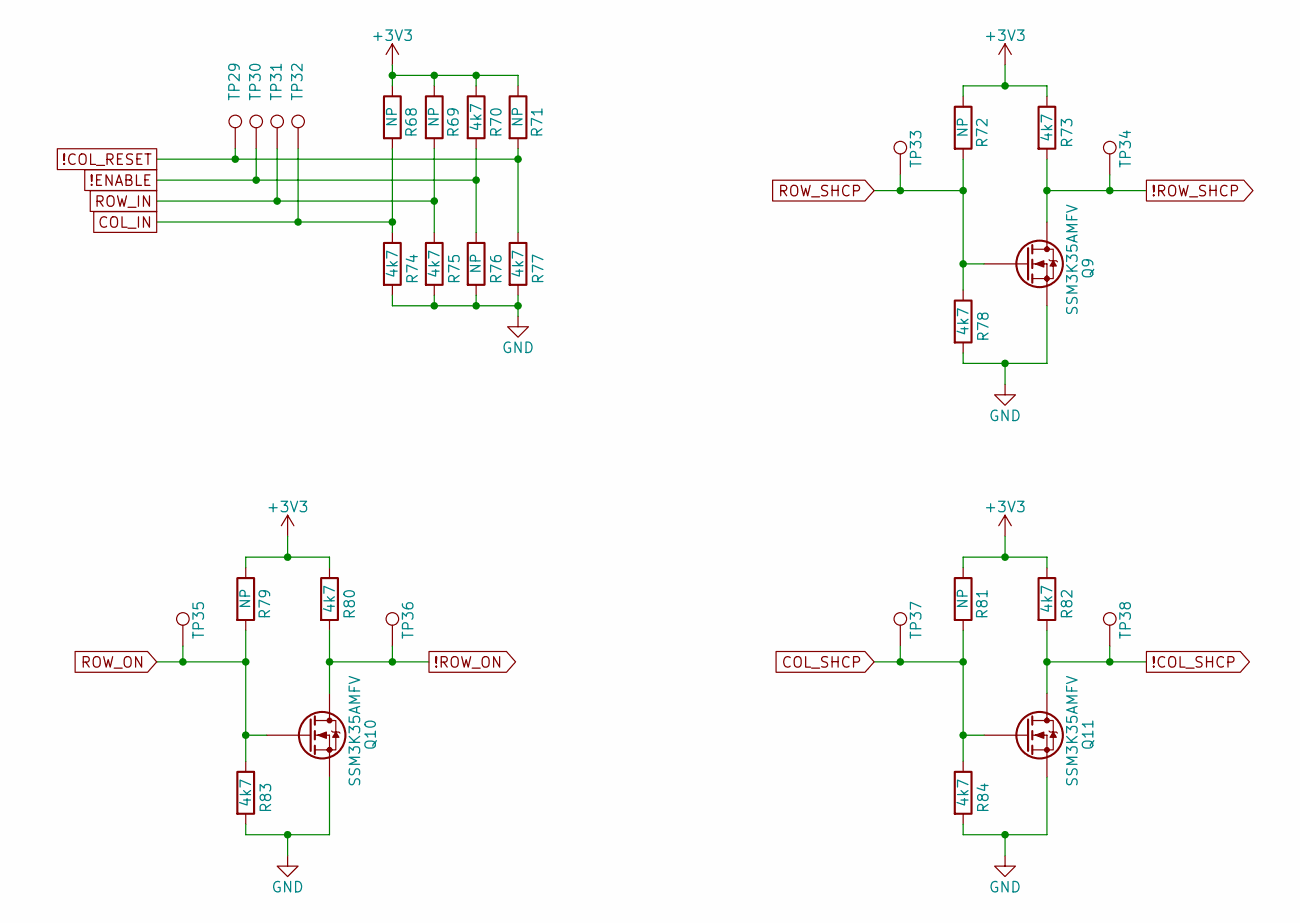
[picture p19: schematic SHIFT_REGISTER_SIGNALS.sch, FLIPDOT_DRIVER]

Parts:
Q9, Q10, Q11: SSM3K35AMFV; SOT-723
R68, R69, R71, R72, R76, R79, R81: NP_R_0603; R_0603_1608Metric
R70, R73, R74, R75, R77, R78, R80, R82, R83, R84: CRG0603F4K7; R_0603_1608Metric; TOLERANCE 5%
TP29, TP30, TP31, TP32, TP33, TP34, TP35, TP36, TP37, TP38: TestPoint; TestPoint_THTPad_D1.0mm_Drill0.5mm

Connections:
!COL_RESET: R71.2, R77.1, TP29.1; also elsewhere on the board
!COL_SHCP: Q11.3 (D), R82.2, TP38.1; also elsewhere on the board
!ENABLE: R70.2, R76.1, TP30.1; also elsewhere on the board
!ROW_ON: Q10.3 (D), R80.2, TP36.1; also elsewhere on the board
!ROW_SHCP: Q9.3 (D), R73.2, TP34.1; also elsewhere on the board
+3V3: R68.1, R69.1, R70.1, R71.1, R72.1, R73.1, R79.1, R80.1, R81.1, R82.1; also elsewhere on the board
COL_IN: R68.2, R74.1, TP32.1; also elsewhere on the board
COL_SHCP: Q11.1 (G), R81.2, R84.1, TP37.1; also elsewhere on the board
GND: Q9.2 (S), Q10.2 (S), Q11.2 (S), R74.2, R75.2, R76.2, R77.2, R78.2, R83.2, R84.2; also elsewhere on the board
ROW_IN: R69.2, R75.1, TP31.1; also elsewhere on the board
ROW_ON: Q10.1 (G), R79.2, R83.1, TP35.1; also elsewhere on the board
ROW_SHCP: Q9.1 (G), R72.2, R78.1, TP33.1; also elsewhere on the board

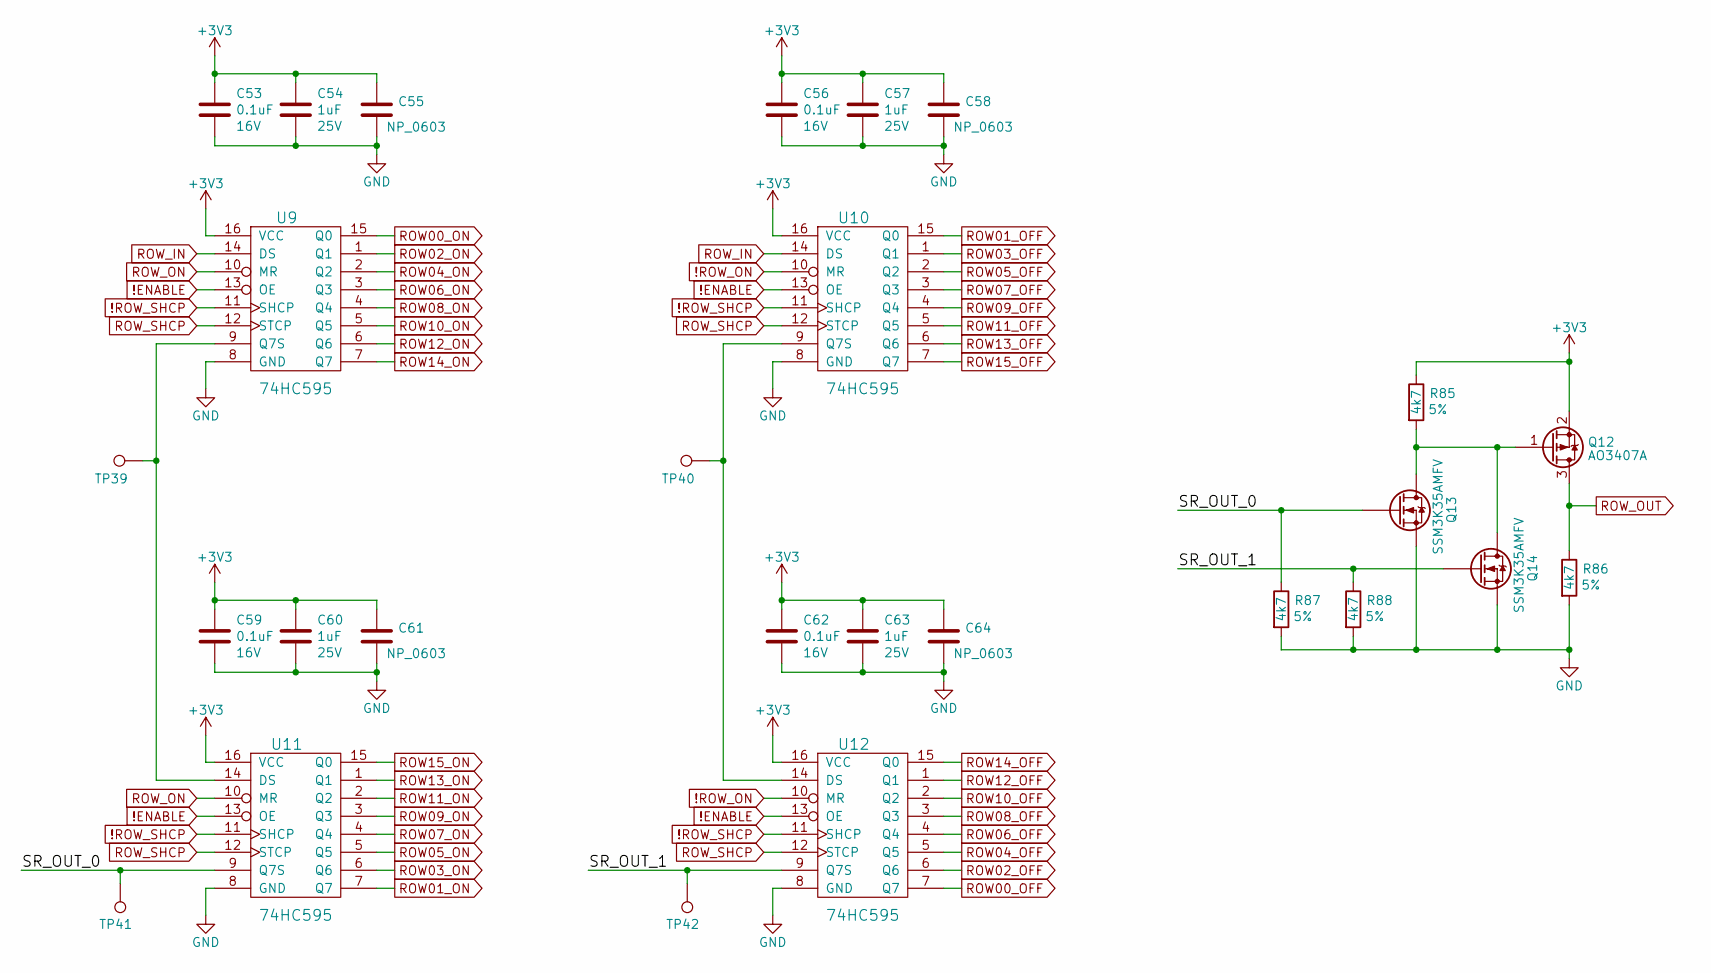
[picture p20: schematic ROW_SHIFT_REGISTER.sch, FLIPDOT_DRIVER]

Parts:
C53, C56, C59, C62: CL10B104KO8NNNC; C_0603_1608Metric; Rating 16V
C54, C57, C60, C63: CL10B105KA8NNNC; C_0603_1608Metric; Rating 25V
C55, C58, C61, C64: NP_0603; C_0603_1608Metric
Q12: AO3407A; SOT-23
Q13, Q14: SSM3K35AMFV; SOT-723
R85, R86, R87, R88: CRG0603F4K7; R_0603_1608Metric; TOLERANCE 5%
TP39, TP40, TP41, TP42: TestPoint; TestPoint_THTPad_D1.0mm_Drill0.5mm
U9, U10, U11, U12: 74HC595; SOIC-16_3.9x9.9mm_P1.27mm

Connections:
!ENABLE: U9.13 (OE), U10.13 (OE), U11.13 (OE), U12.13 (OE); also elsewhere on the board
!ROW_ON: U10.10 (MR), U12.10 (MR); also elsewhere on the board
!ROW_SHCP: U9.11 (SHCP), U10.11 (SHCP), U11.11 (SHCP), U12.11 (SHCP); also elsewhere on the board
+3V3: C53.1, C54.1, C55.1, C56.1, C57.1, C58.1, C59.1, C60.1, C61.1, C62.1, C63.1, C64.1, Q12.2 (S), R85.1, U9.16 (VCC), U10.16 (VCC), U11.16 (VCC), U12.16 (VCC); also elsewhere on the board
/ROW_SHIFT_REGISTER/SR_OUT_0: Q13.1 (G), R87.1, TP41.1, U11.9 (Q7S)
/ROW_SHIFT_REGISTER/SR_OUT_1: Q14.1 (G), R88.1, TP42.1, U12.9 (Q7S)
GND: C53.2, C54.2, C55.2, C56.2, C57.2, C58.2, C59.2, C60.2, C61.2, C62.2, C63.2, C64.2, Q13.2 (S), Q14.2 (S), R86.2, R87.2, R88.2, U9.8 (GND), U10.8 (GND), U11.8 (GND), U12.8 (GND); also elsewhere on the board
unnamed: Q12.1 (G), Q13.3 (D), Q14.3 (D), R85.2
unnamed: TP39.1, U9.9 (Q7S), U11.14 (DS)
unnamed: TP40.1, U10.9 (Q7S), U12.14 (DS)
ROW00_OFF: U12.7 (Q7); also elsewhere on the board
ROW00_ON: U9.15 (Q0); also elsewhere on the board
ROW01_OFF: U10.15 (Q0); also elsewhere on the board
ROW01_ON: U11.7 (Q7); also elsewhere on the board
ROW02_OFF: U12.6 (Q6); also elsewhere on the board
ROW02_ON: U9.1 (Q1); also elsewhere on the board
ROW03_OFF: U10.1 (Q1); also elsewhere on the board
ROW03_ON: U11.6 (Q6); also elsewhere on the board
ROW04_OFF: U12.5 (Q5); also elsewhere on the board
ROW04_ON: U9.2 (Q2); also elsewhere on the board
ROW05_OFF: U10.2 (Q2); also elsewhere on the board
ROW05_ON: U11.5 (Q5); also elsewhere on the board
ROW06_OFF: U12.4 (Q4); also elsewhere on the board
ROW06_ON: U9.3 (Q3); also elsewhere on the board
ROW07_OFF: U10.3 (Q3); also elsewhere on the board
ROW07_ON: U11.4 (Q4); also elsewhere on the board
ROW08_OFF: U12.3 (Q3); also elsewhere on the board
ROW08_ON: U9.4 (Q4); also elsewhere on the board
ROW09_OFF: U10.4 (Q4); also elsewhere on the board
ROW09_ON: U11.3 (Q3); also elsewhere on the board
ROW10_OFF: U12.2 (Q2); also elsewhere on the board
ROW10_ON: U9.5 (Q5); also elsewhere on the board
ROW11_OFF: U10.5 (Q5); also elsewhere on the board
ROW11_ON: U11.2 (Q2); also elsewhere on the board
ROW12_OFF: U12.1 (Q1); also elsewhere on the board
ROW12_ON: U9.6 (Q6); also elsewhere on the board
ROW13_OFF: U10.6 (Q6); also elsewhere on the board
ROW13_ON: U11.1 (Q1); also elsewhere on the board
ROW14_OFF: U12.15 (Q0); also elsewhere on the board
ROW14_ON: U9.7 (Q7); also elsewhere on the board
ROW15_OFF: U10.7 (Q7); also elsewhere on the board
ROW15_ON: U11.15 (Q0); also elsewhere on the board
ROW_IN: U9.14 (DS), U10.14 (DS); also elsewhere on the board
ROW_ON: U9.10 (MR), U11.10 (MR); also elsewhere on the board
ROW_OUT: Q12.3 (D), R86.1; also elsewhere on the board
ROW_SHCP: U9.12 (STCP), U10.12 (STCP), U11.12 (STCP), U12.12 (STCP); also elsewhere on the board

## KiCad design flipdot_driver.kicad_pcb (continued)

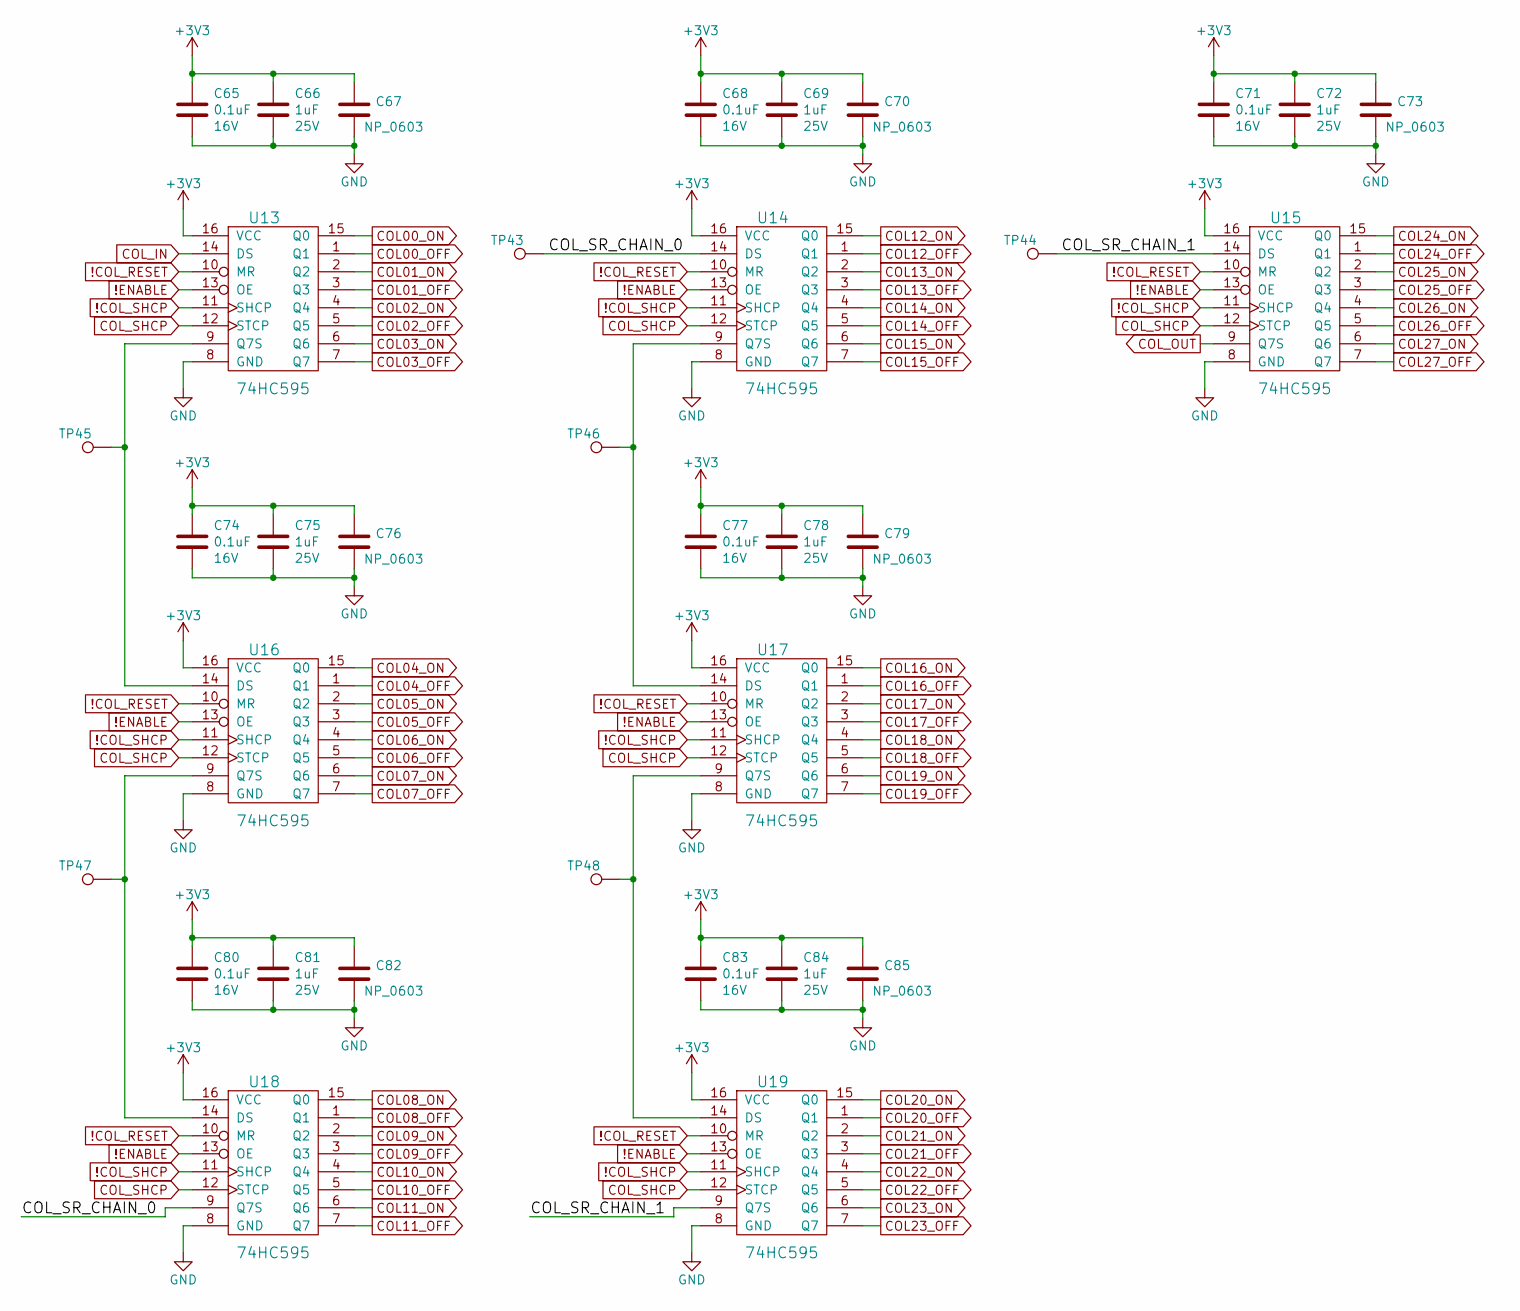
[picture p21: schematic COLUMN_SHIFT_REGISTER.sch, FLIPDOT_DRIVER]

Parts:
C65, C68, C71, C74, C77, C80, C83: CL10B104KO8NNNC; C_0603_1608Metric; Rating 16V
C66, C69, C72, C75, C78, C81, C84: CL10B105KA8NNNC; C_0603_1608Metric; Rating 25V
C67, C70, C73, C76, C79, C82, C85: NP_0603; C_0603_1608Metric
TP43, TP44, TP45, TP46, TP47, TP48: TestPoint; TestPoint_THTPad_D1.0mm_Drill0.5mm
U13, U14, U15, U16, U17, U18, U19: 74HC595; SOIC-16_3.9x9.9mm_P1.27mm

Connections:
!COL_RESET: U13.10 (MR), U14.10 (MR), U15.10 (MR), U16.10 (MR), U17.10 (MR), U18.10 (MR), U19.10 (MR); also elsewhere on the board
!COL_SHCP: U13.11 (SHCP), U14.11 (SHCP), U15.11 (SHCP), U16.11 (SHCP), U17.11 (SHCP), U18.11 (SHCP), U19.11 (SHCP); also elsewhere on the board
!ENABLE: U13.13 (OE), U14.13 (OE), U15.13 (OE), U16.13 (OE), U17.13 (OE), U18.13 (OE), U19.13 (OE); also elsewhere on the board
+3V3: C65.1, C66.1, C67.1, C68.1, C69.1, C70.1, C71.1, C72.1, C73.1, C74.1, C75.1, C76.1, C77.1, C78.1, C79.1, C80.1, C81.1, C82.1, C83.1, C84.1, C85.1, U13.16 (VCC), U14.16 (VCC), U15.16 (VCC), U16.16 (VCC), U17.16 (VCC), U18.16 (VCC), U19.16 (VCC); also elsewhere on the board
/COLUMN_SHIFT_REGISTER/COL_SR_CHAIN_0: TP43.1, U14.14 (DS), U18.9 (Q7S)
/COLUMN_SHIFT_REGISTER/COL_SR_CHAIN_1: TP44.1, U15.14 (DS), U19.9 (Q7S)
COL00_OFF: U13.1 (Q1); also elsewhere on the board
COL00_ON: U13.15 (Q0); also elsewhere on the board
COL01_OFF: U13.3 (Q3); also elsewhere on the board
COL01_ON: U13.2 (Q2); also elsewhere on the board
COL02_OFF: U13.5 (Q5); also elsewhere on the board
COL02_ON: U13.4 (Q4); also elsewhere on the board
COL03_OFF: U13.7 (Q7); also elsewhere on the board
COL03_ON: U13.6 (Q6); also elsewhere on the board
COL04_OFF: U16.1 (Q1); also elsewhere on the board
COL04_ON: U16.15 (Q0); also elsewhere on the board
COL05_OFF: U16.3 (Q3); also elsewhere on the board
COL05_ON: U16.2 (Q2); also elsewhere on the board
COL06_OFF: U16.5 (Q5); also elsewhere on the board
COL06_ON: U16.4 (Q4); also elsewhere on the board
COL07_OFF: U16.7 (Q7); also elsewhere on the board
COL07_ON: U16.6 (Q6); also elsewhere on the board
COL08_OFF: U18.1 (Q1); also elsewhere on the board
COL08_ON: U18.15 (Q0); also elsewhere on the board
COL09_OFF: U18.3 (Q3); also elsewhere on the board
COL09_ON: U18.2 (Q2); also elsewhere on the board
COL10_OFF: U18.5 (Q5); also elsewhere on the board
COL10_ON: U18.4 (Q4); also elsewhere on the board
COL11_OFF: U18.7 (Q7); also elsewhere on the board
COL11_ON: U18.6 (Q6); also elsewhere on the board
COL12_OFF: U14.1 (Q1); also elsewhere on the board
COL12_ON: U14.15 (Q0); also elsewhere on the board
COL13_OFF: U14.3 (Q3); also elsewhere on the board
COL13_ON: U14.2 (Q2); also elsewhere on the board
COL14_OFF: U14.5 (Q5); also elsewhere on the board
COL14_ON: U14.4 (Q4); also elsewhere on the board
COL15_OFF: U14.7 (Q7); also elsewhere on the board
COL15_ON: U14.6 (Q6); also elsewhere on the board
COL16_OFF: U17.1 (Q1); also elsewhere on the board
COL16_ON: U17.15 (Q0); also elsewhere on the board
COL17_OFF: U17.3 (Q3); also elsewhere on the board
COL17_ON: U17.2 (Q2); also elsewhere on the board
COL18_OFF: U17.5 (Q5); also elsewhere on the board
COL18_ON: U17.4 (Q4); also elsewhere on the board
COL19_OFF: U17.7 (Q7); also elsewhere on the board
COL19_ON: U17.6 (Q6); also elsewhere on the board
COL20_OFF: U19.1 (Q1); also elsewhere on the board
COL20_ON: U19.15 (Q0); also elsewhere on the board
COL21_OFF: U19.3 (Q3); also elsewhere on the board
COL21_ON: U19.2 (Q2); also elsewhere on the board
COL22_OFF: U19.5 (Q5); also elsewhere on the board
COL22_ON: U19.4 (Q4); also elsewhere on the board
COL23_OFF: U19.7 (Q7); also elsewhere on the board
COL23_ON: U19.6 (Q6); also elsewhere on the board
COL24_OFF: U15.1 (Q1); also elsewhere on the board
COL24_ON: U15.15 (Q0); also elsewhere on the board
COL25_OFF: U15.3 (Q3); also elsewhere on the board
COL25_ON: U15.2 (Q2); also elsewhere on the board
COL26_OFF: U15.5 (Q5); also elsewhere on the board
COL26_ON: U15.4 (Q4); also elsewhere on the board
COL27_OFF: U15.7 (Q7); also elsewhere on the board
COL27_ON: U15.6 (Q6); also elsewhere on the board
COL_IN: U13.14 (DS); also elsewhere on the board
COL_OUT: U15.9 (Q7S); also elsewhere on the board
COL_SHCP: U13.12 (STCP), U14.12 (STCP), U15.12 (STCP), U16.12 (STCP), U17.12 (STCP), U18.12 (STCP), U19.12 (STCP); also elsewhere on the board
GND: C65.2, C66.2, C67.2, C68.2, C69.2, C70.2, C71.2, C72.2, C73.2, C74.2, C75.2, C76.2, C77.2, C78.2, C79.2, C80.2, C81.2, C82.2, C83.2, C84.2, C85.2, U13.8 (GND), U14.8 (GND), U15.8 (GND), U16.8 (GND), U17.8 (GND), U18.8 (GND), U19.8 (GND); also elsewhere on the board
unnamed: TP45.1, U13.9 (Q7S), U16.14 (DS)
unnamed: TP46.1, U14.9 (Q7S), U17.14 (DS)
unnamed: TP47.1, U16.9 (Q7S), U18.14 (DS)
unnamed: TP48.1, U17.9 (Q7S), U19.14 (DS)

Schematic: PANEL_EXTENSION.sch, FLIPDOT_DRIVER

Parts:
C86, C87: CL10B104KO8NNNC; C_0603_1608Metric; Rating 16V
J10: Conn_01x08_Male; PinHeader_1x08_P2.54mm_Horizontal
R89, R90, R91, R92: CRG0603F4K7; R_0603_1608Metric; TOLERANCE 5%
TP49, TP50, TP51, TP52, TP53, TP54, TP55, TP56, TP57, TP58, TP59, TP60: TestPoint; TestPoint_THTPad_D1.0mm_Drill0.5mm
U20, U22: SGM3157YC6; SOT-363_SC-70-6
U21, U23: CM1293A-04SO; SOT-457

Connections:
!COL_RESET: J10.3, TP58.1, U23.3 (CH2); also elsewhere on the board
!ENABLE: J10.2, TP59.1, U23.4 (CH3); also elsewhere on the board
+3V3: C86.1, C87.1, U20.5 (VCC), U21.5 (V+), U22.5 (VCC), U23.5 (V+); also elsewhere on the board
/PANEL_EXTENSION/COL_DATA: J10.5, R91.1, TP56.1, U21.6 (CH4), U22.4 (COM)
/PANEL_EXTENSION/ROW_DATA: J10.8, R89.1, TP53.1, U20.4 (COM), U21.1 (CH1)
COL_IN: TP52.1, U22.3 (N_OP); also elsewhere on the board
COL_MODE_SEL: R92.1, U22.6 (IN); also elsewhere on the board
COL_OUT: TP51.1, U22.1 (N_CL); also elsewhere on the board
COL_SHCP: J10.4, TP57.1, U23.1 (CH1); also elsewhere on the board
GND: C86.2, C87.2, J10.1, R89.2, R90.2, R91.2, R92.2, TP60.1, U20.2 (GND), U21.2 (V-), U22.2 (GND), U23.2 (V-), U23.6 (CH4); also elsewhere on the board
ROW_IN: TP50.1, U20.3 (N_OP); also elsewhere on the board
ROW_MODE_SEL: R90.1, U20.6 (IN); also elsewhere on the board
ROW_ON: J10.6, TP55.1, U21.4 (CH3); also elsewhere on the board
ROW_OUT: TP49.1, U20.1 (N_CL); also elsewhere on the board
ROW_SHCP: J10.7, TP54.1, U21.3 (CH2); also elsewhere on the board

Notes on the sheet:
CONN_GND

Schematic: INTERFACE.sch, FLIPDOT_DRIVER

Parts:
J11: 3x32_1&3_loaded_2.5mm_0.1in_female_header; 32x3_POP_1_3
Q15: DMG6602; TSOT-23-6
R93: CRG0603F4K7; R_0603_1608Metric; TOLERANCE 5%
TP61, TP62: TestPoint; TestPoint_THTPad_D1.0mm_Drill0.5mm

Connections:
+24V: J11.3, J11.4; also elsewhere on the board
COL00: J11.37; also elsewhere on the board
COL01: J11.38; also elsewhere on the board
COL02: J11.39; also elsewhere on the board
COL03: J11.40; also elsewhere on the board
COL04: J11.41; also elsewhere on the board
COL05: J11.42; also elsewhere on the board
COL06: J11.43; also elsewhere on the board
COL07: J11.44; also elsewhere on the board
COL08: J11.45; also elsewhere on the board
COL09: J11.46; also elsewhere on the board
COL10: J11.47; also elsewhere on the board
COL11: J11.48; also elsewhere on the board
COL12: J11.49; also elsewhere on the board
COL13: J11.50; also elsewhere on the board
COL14: J11.51; also elsewhere on the board
COL15: J11.52; also elsewhere on the board
COL16: J11.53; also elsewhere on the board
COL17: J11.54; also elsewhere on the board
COL18: J11.55; also elsewhere on the board
COL19: J11.56; also elsewhere on the board
COL20: J11.57; also elsewhere on the board
COL21: J11.58; also elsewhere on the board
COL22: J11.59; also elsewhere on the board
COL23: J11.60; also elsewhere on the board
COL24: J11.61; also elsewhere on the board
COL25: J11.62; also elsewhere on the board
COL26: J11.63; also elsewhere on the board
COL27: J11.64; also elsewhere on the board
GND: Q15.5 (S), R93.2; also elsewhere on the board
LED_PWM: Q15.1 (G), R93.1, TP62.1; also elsewhere on the board
unnamed: J11.1, J11.2, Q15.6 (D), TP61.1
ROW00N: J11.36; also elsewhere on the board
ROW00P: J11.35; also elsewhere on the board
ROW01N: J11.6; also elsewhere on the board
ROW01P: J11.5; also elsewhere on the board
ROW02N: J11.34; also elsewhere on the board
ROW02P: J11.33; also elsewhere on the board
ROW03N: J11.8; also elsewhere on the board
ROW03P: J11.7; also elsewhere on the board
ROW04N: J11.32; also elsewhere on the board
ROW04P: J11.31; also elsewhere on the board
ROW05N: J11.10; also elsewhere on the board
ROW05P: J11.9; also elsewhere on the board
ROW06N: J11.30; also elsewhere on the board
ROW06P: J11.29; also elsewhere on the board
ROW07N: J11.12; also elsewhere on the board
ROW07P: J11.11; also elsewhere on the board
ROW08N: J11.28; also elsewhere on the board
ROW08P: J11.27; also elsewhere on the board
ROW09N: J11.14; also elsewhere on the board
ROW09P: J11.13; also elsewhere on the board
ROW10N: J11.26; also elsewhere on the board
ROW10P: J11.25; also elsewhere on the board
ROW11N: J11.16; also elsewhere on the board
ROW11P: J11.15; also elsewhere on the board
ROW12N: J11.24; also elsewhere on the board
ROW12P: J11.23; also elsewhere on the board
ROW13N: J11.18; also elsewhere on the board
ROW13P: J11.17; also elsewhere on the board
ROW14N: J11.22; also elsewhere on the board
ROW14P: J11.21; also elsewhere on the board
ROW15N: J11.20; also elsewhere on the board
ROW15P: J11.19; also elsewhere on the board

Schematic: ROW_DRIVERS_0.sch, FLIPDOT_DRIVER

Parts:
D18, D19, D20, D21, D22, D23, D24, D25: MMBZ5243BLT1G; SOT-23; Rating 13V
Q16, Q17, Q20, Q21: DMG6602; TSOT-23-6
Q18, Q19, Q22, Q23: SSM3K35AMFV; SOT-723
R94, R95, R96, R97, R98, R99, R100, R101, R102, R103, R104, R105: CRG0603F4K7; R_0603_1608Metric; TOLERANCE 5%
TP63, TP64, TP66, TP68, TP70, TP72, TP74: TestPoint; TestPoint_THTPad_D1.0mm_Drill0.5mm

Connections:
+12V: D18.1 (K), D19.1 (K), D22.1 (K), D23.1 (K), Q16.2 (S), Q17.2 (S), Q20.2 (S), Q21.2 (S), R94.1, R95.1, R100.1, R101.1, TP63.1; also elsewhere on the board
GND: D20.2 (A), D21.2 (A), D24.2 (A), D25.2 (A), Q16.5 (S), Q17.5 (S), Q18.2 (S), Q19.2 (S), Q20.5 (S), Q21.5 (S), Q22.2 (S), Q23.2 (S), R96.2, R97.2, R98.2, R99.2, R102.2, R103.2, R104.2, R105.2, TP70.1; also elsewhere on the board
unnamed: Q16.3 (G), Q18.3 (D), R94.2, TP64.1
unnamed: Q17.3 (G), Q19.3 (D), R95.2
unnamed: Q20.3 (G), Q22.3 (D), R100.2
unnamed: Q21.3 (G), Q23.3 (D), R101.2
ROW00N: D20.1 (K), Q16.6 (D), TP72.1; also elsewhere on the board
ROW00P: D18.2 (A), Q16.4 (D), TP68.1; also elsewhere on the board
ROW00_OFF: Q16.1 (G), R98.1, TP74.1; also elsewhere on the board
ROW00_ON: Q18.1 (G), R96.1, TP66.1; also elsewhere on the board
ROW01N: D21.1 (K), Q17.6 (D); also elsewhere on the board
ROW01P: D19.2 (A), Q17.4 (D); also elsewhere on the board
ROW01_OFF: Q17.1 (G), R99.1; also elsewhere on the board
ROW01_ON: Q19.1 (G), R97.1; also elsewhere on the board
ROW02N: D24.1 (K), Q20.6 (D); also elsewhere on the board
ROW02P: D22.2 (A), Q20.4 (D); also elsewhere on the board
ROW02_OFF: Q20.1 (G), R104.1; also elsewhere on the board
ROW02_ON: Q22.1 (G), R102.1; also elsewhere on the board
ROW03N: D25.1 (K), Q21.6 (D); also elsewhere on the board
ROW03P: D23.2 (A), Q21.4 (D); also elsewhere on the board
ROW03_OFF: Q21.1 (G), R105.1; also elsewhere on the board
ROW03_ON: Q23.1 (G), R103.1; also elsewhere on the board

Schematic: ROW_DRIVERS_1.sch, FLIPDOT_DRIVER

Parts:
D26, D27, D28, D29, D30, D31, D32, D33: MMBZ5243BLT1G; SOT-23; Rating 13V
Q24, Q25, Q28, Q29: DMG6602; TSOT-23-6
Q26, Q27, Q30, Q31: SSM3K35AMFV; SOT-723
R106, R107, R108, R109, R110, R111, R112, R113, R114, R115, R116, R117: CRG0603F4K7; R_0603_1608Metric; TOLERANCE 5%

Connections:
+12V: D26.1 (K), D27.1 (K), D30.1 (K), D31.1 (K), Q24.2 (S), Q25.2 (S), Q28.2 (S), Q29.2 (S), R106.1, R107.1, R112.1, R113.1; also elsewhere on the board
GND: D28.2 (A), D29.2 (A), D32.2 (A), D33.2 (A), Q24.5 (S), Q25.5 (S), Q26.2 (S), Q27.2 (S), Q28.5 (S), Q29.5 (S), Q30.2 (S), Q31.2 (S), R108.2, R109.2, R110.2, R111.2, R114.2, R115.2, R116.2, R117.2; also elsewhere on the board
unnamed: Q24.3 (G), Q26.3 (D), R106.2
unnamed: Q25.3 (G), Q27.3 (D), R107.2
unnamed: Q28.3 (G), Q30.3 (D), R112.2
unnamed: Q29.3 (G), Q31.3 (D), R113.2
ROW04N: D28.1 (K), Q24.6 (D); also elsewhere on the board
ROW04P: D26.2 (A), Q24.4 (D); also elsewhere on the board
ROW04_OFF: Q24.1 (G), R110.1; also elsewhere on the board
ROW04_ON: Q26.1 (G), R108.1; also elsewhere on the board
ROW05N: D29.1 (K), Q25.6 (D); also elsewhere on the board
ROW05P: D27.2 (A), Q25.4 (D); also elsewhere on the board
ROW05_OFF: Q25.1 (G), R111.1; also elsewhere on the board
ROW05_ON: Q27.1 (G), R109.1; also elsewhere on the board
ROW06N: D32.1 (K), Q28.6 (D); also elsewhere on the board
ROW06P: D30.2 (A), Q28.4 (D); also elsewhere on the board
ROW06_OFF: Q28.1 (G), R116.1; also elsewhere on the board
ROW06_ON: Q30.1 (G), R114.1; also elsewhere on the board
ROW07N: D33.1 (K), Q29.6 (D); also elsewhere on the board
ROW07P: D31.2 (A), Q29.4 (D); also elsewhere on the board
ROW07_OFF: Q29.1 (G), R117.1; also elsewhere on the board
ROW07_ON: Q31.1 (G), R115.1; also elsewhere on the board

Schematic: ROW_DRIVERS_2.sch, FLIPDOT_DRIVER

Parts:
D34, D35, D36, D37, D38, D39, D40, D41: MMBZ5243BLT1G; SOT-23; Rating 13V
Q32, Q33, Q36, Q37: DMG6602; TSOT-23-6
Q34, Q35, Q38, Q39: SSM3K35AMFV; SOT-723
R118, R119, R120, R121, R122, R123, R124, R125, R126, R127, R128, R129: CRG0603F4K7; R_0603_1608Metric; TOLERANCE 5%

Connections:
+12V: D34.1 (K), D35.1 (K), D38.1 (K), D39.1 (K), Q32.2 (S), Q33.2 (S), Q36.2 (S), Q37.2 (S), R118.1, R119.1, R124.1, R125.1; also elsewhere on the board
GND: D36.2 (A), D37.2 (A), D40.2 (A), D41.2 (A), Q32.5 (S), Q33.5 (S), Q34.2 (S), Q35.2 (S), Q36.5 (S), Q37.5 (S), Q38.2 (S), Q39.2 (S), R120.2, R121.2, R122.2, R123.2, R126.2, R127.2, R128.2, R129.2; also elsewhere on the board
unnamed: Q32.3 (G), Q34.3 (D), R118.2
unnamed: Q33.3 (G), Q35.3 (D), R119.2
unnamed: Q36.3 (G), Q38.3 (D), R124.2
unnamed: Q37.3 (G), Q39.3 (D), R125.2
ROW08N: D36.1 (K), Q32.6 (D); also elsewhere on the board
ROW08P: D34.2 (A), Q32.4 (D); also elsewhere on the board
ROW08_OFF: Q32.1 (G), R122.1; also elsewhere on the board
ROW08_ON: Q34.1 (G), R120.1; also elsewhere on the board
ROW09N: D37.1 (K), Q33.6 (D); also elsewhere on the board
ROW09P: D35.2 (A), Q33.4 (D); also elsewhere on the board
ROW09_OFF: Q33.1 (G), R123.1; also elsewhere on the board
ROW09_ON: Q35.1 (G), R121.1; also elsewhere on the board
ROW10N: D40.1 (K), Q36.6 (D); also elsewhere on the board
ROW10P: D38.2 (A), Q36.4 (D); also elsewhere on the board
ROW10_OFF: Q36.1 (G), R128.1; also elsewhere on the board
ROW10_ON: Q38.1 (G), R126.1; also elsewhere on the board
ROW11N: D41.1 (K), Q37.6 (D); also elsewhere on the board
ROW11P: D39.2 (A), Q37.4 (D); also elsewhere on the board
ROW11_OFF: Q37.1 (G), R129.1; also elsewhere on the board
ROW11_ON: Q39.1 (G), R127.1; also elsewhere on the board

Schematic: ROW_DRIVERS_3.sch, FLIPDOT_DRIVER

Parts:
D42, D43, D44, D45, D46, D47, D48, D49: MMBZ5243BLT1G; SOT-23; Rating 13V
Q40, Q41, Q44, Q45: DMG6602; TSOT-23-6
Q42, Q43, Q46, Q47: SSM3K35AMFV; SOT-723
R130, R131, R132, R133, R134, R135, R136, R137, R138, R139, R140, R141: CRG0603F4K7; R_0603_1608Metric; TOLERANCE 5%

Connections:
+12V: D42.1 (K), D43.1 (K), D46.1 (K), D47.1 (K), Q40.2 (S), Q41.2 (S), Q44.2 (S), Q45.2 (S), R130.1, R131.1, R136.1, R137.1; also elsewhere on the board
GND: D44.2 (A), D45.2 (A), D48.2 (A), D49.2 (A), Q40.5 (S), Q41.5 (S), Q42.2 (S), Q43.2 (S), Q44.5 (S), Q45.5 (S), Q46.2 (S), Q47.2 (S), R132.2, R133.2, R134.2, R135.2, R138.2, R139.2, R140.2, R141.2; also elsewhere on the board
unnamed: Q40.3 (G), Q42.3 (D), R130.2
unnamed: Q41.3 (G), Q43.3 (D), R131.2
unnamed: Q44.3 (G), Q46.3 (D), R136.2
unnamed: Q45.3 (G), Q47.3 (D), R137.2
ROW12N: D44.1 (K), Q40.6 (D); also elsewhere on the board
ROW12P: D42.2 (A), Q40.4 (D); also elsewhere on the board
ROW12_OFF: Q40.1 (G), R134.1; also elsewhere on the board
ROW12_ON: Q42.1 (G), R132.1; also elsewhere on the board
ROW13N: D45.1 (K), Q41.6 (D); also elsewhere on the board
ROW13P: D43.2 (A), Q41.4 (D); also elsewhere on the board
ROW13_OFF: Q41.1 (G), R135.1; also elsewhere on the board
ROW13_ON: Q43.1 (G), R133.1; also elsewhere on the board
ROW14N: D48.1 (K), Q44.6 (D); also elsewhere on the board
ROW14P: D46.2 (A), Q44.4 (D); also elsewhere on the board
ROW14_OFF: Q44.1 (G), R140.1; also elsewhere on the board
ROW14_ON: Q46.1 (G), R138.1; also elsewhere on the board
ROW15N: D49.1 (K), Q45.6 (D); also elsewhere on the board
ROW15P: D47.2 (A), Q45.4 (D); also elsewhere on the board
ROW15_OFF: Q45.1 (G), R141.1; also elsewhere on the board
ROW15_ON: Q47.1 (G), R139.1; also elsewhere on the board

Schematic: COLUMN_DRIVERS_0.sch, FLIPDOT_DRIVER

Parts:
Q48, Q49, Q50, Q57, Q58, Q59: DMG6602; TSOT-23-6
Q51, Q52, Q53, Q54, Q55, Q56, Q60, Q61, Q62, Q63, Q64, Q65: SSM3K35AMFV; SOT-723
R142, R143, R144, R145, R146, R147, R148, R149, R150, R151, R152, R153, R154, R155, R156, R157, R158, R159, R160, R161, R162, R163, R164, R165: CRG0603F4K7; R_0603_1608Metric; TOLERANCE 5%
TP78, TP80, TP82, TP83, TP84, TP88, TP90: TestPoint; TestPoint_THTPad_D1.0mm_Drill0.5mm

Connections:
+12V: Q48.2 (S), Q49.2 (S), Q50.2 (S), Q57.2 (S), Q58.2 (S), Q59.2 (S), R142.1, R143.1, R144.1, R154.1, R155.1, R156.1, TP78.1; also elsewhere on the board
COL00: Q48.4 (D), Q48.6 (D), TP84.1; also elsewhere on the board
COL00_OFF: R145.2, R149.1, TP82.1; also elsewhere on the board
COL00_ON: Q51.1 (G), Q54.1 (G), R148.1, TP83.1; also elsewhere on the board
COL01: Q49.4 (D), Q49.6 (D); also elsewhere on the board
COL01_OFF: R146.2, R151.1; also elsewhere on the board
COL01_ON: Q52.1 (G), Q55.1 (G), R150.1; also elsewhere on the board
COL02: Q50.4 (D), Q50.6 (D); also elsewhere on the board
COL02_OFF: R147.2, R153.1; also elsewhere on the board
COL02_ON: Q53.1 (G), Q56.1 (G), R152.1; also elsewhere on the board
COL03: Q57.4 (D), Q57.6 (D); also elsewhere on the board
COL03_OFF: R157.2, R161.1; also elsewhere on the board
COL03_ON: Q60.1 (G), Q63.1 (G), R160.1; also elsewhere on the board
COL04: Q58.4 (D), Q58.6 (D); also elsewhere on the board
COL04_OFF: R158.2, R163.1; also elsewhere on the board
COL04_ON: Q61.1 (G), Q64.1 (G), R162.1; also elsewhere on the board
COL05: Q59.4 (D), Q59.6 (D); also elsewhere on the board
COL05_OFF: R159.2, R165.1; also elsewhere on the board
COL05_ON: Q62.1 (G), Q65.1 (G), R164.1; also elsewhere on the board
GND: Q48.5 (S), Q49.5 (S), Q50.5 (S), Q51.2 (S), Q52.2 (S), Q53.2 (S), Q54.2 (S), Q55.2 (S), Q56.2 (S), Q57.5 (S), Q58.5 (S), Q59.5 (S), Q60.2 (S), Q61.2 (S), Q62.2 (S), Q63.2 (S), Q64.2 (S), Q65.2 (S), R148.2, R149.2, R150.2, R151.2, R152.2, R153.2, R160.2, R161.2, R162.2, R163.2, R164.2, R165.2, TP90.1; also elsewhere on the board
unnamed: Q48.1 (G), Q54.3 (D), R145.1, TP88.1
unnamed: Q48.3 (G), Q51.3 (D), R142.2, TP80.1
unnamed: Q49.1 (G), Q55.3 (D), R146.1
unnamed: Q49.3 (G), Q52.3 (D), R143.2
unnamed: Q50.1 (G), Q56.3 (D), R147.1
unnamed: Q50.3 (G), Q53.3 (D), R144.2
unnamed: Q57.1 (G), Q63.3 (D), R157.1
unnamed: Q57.3 (G), Q60.3 (D), R154.2
unnamed: Q58.1 (G), Q64.3 (D), R158.1
unnamed: Q58.3 (G), Q61.3 (D), R155.2
unnamed: Q59.1 (G), Q65.3 (D), R159.1
unnamed: Q59.3 (G), Q62.3 (D), R156.2

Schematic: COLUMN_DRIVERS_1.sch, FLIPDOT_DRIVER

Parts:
Q66, Q67, Q68, Q75, Q76, Q77: DMG6602; TSOT-23-6
Q69, Q70, Q71, Q72, Q73, Q74, Q78, Q79, Q80, Q81, Q82, Q83: SSM3K35AMFV; SOT-723
R166, R167, R168, R169, R170, R171, R172, R173, R174, R175, R176, R177, R178, R179, R180, R181, R182, R183, R184, R185, R186, R187, R188, R189: CRG0603F4K7; R_0603_1608Metric; TOLERANCE 5%

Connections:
+12V: Q66.2 (S), Q67.2 (S), Q68.2 (S), Q75.2 (S), Q76.2 (S), Q77.2 (S), R166.1, R167.1, R168.1, R178.1, R179.1, R180.1; also elsewhere on the board
COL06: Q66.4 (D), Q66.6 (D); also elsewhere on the board
COL06_OFF: R169.2, R173.1; also elsewhere on the board
COL06_ON: Q69.1 (G), Q72.1 (G), R172.1; also elsewhere on the board
COL07: Q67.4 (D), Q67.6 (D); also elsewhere on the board
COL07_OFF: R170.2, R175.1; also elsewhere on the board
COL07_ON: Q70.1 (G), Q73.1 (G), R174.1; also elsewhere on the board
COL08: Q68.4 (D), Q68.6 (D); also elsewhere on the board
COL08_OFF: R171.2, R177.1; also elsewhere on the board
COL08_ON: Q71.1 (G), Q74.1 (G), R176.1; also elsewhere on the board
COL09: Q75.4 (D), Q75.6 (D); also elsewhere on the board
COL09_OFF: R181.2, R185.1; also elsewhere on the board
COL09_ON: Q78.1 (G), Q81.1 (G), R184.1; also elsewhere on the board
COL10: Q76.4 (D), Q76.6 (D); also elsewhere on the board
COL10_OFF: R182.2, R187.1; also elsewhere on the board
COL10_ON: Q79.1 (G), Q82.1 (G), R186.1; also elsewhere on the board
COL11: Q77.4 (D), Q77.6 (D); also elsewhere on the board
COL11_OFF: R183.2, R189.1; also elsewhere on the board
COL11_ON: Q80.1 (G), Q83.1 (G), R188.1; also elsewhere on the board
GND: Q66.5 (S), Q67.5 (S), Q68.5 (S), Q69.2 (S), Q70.2 (S), Q71.2 (S), Q72.2 (S), Q73.2 (S), Q74.2 (S), Q75.5 (S), Q76.5 (S), Q77.5 (S), Q78.2 (S), Q79.2 (S), Q80.2 (S), Q81.2 (S), Q82.2 (S), Q83.2 (S), R172.2, R173.2, R174.2, R175.2, R176.2, R177.2, R184.2, R185.2, R186.2, R187.2, R188.2, R189.2; also elsewhere on the board
unnamed: Q66.1 (G), Q72.3 (D), R169.1
unnamed: Q66.3 (G), Q69.3 (D), R166.2
unnamed: Q67.1 (G), Q73.3 (D), R170.1
unnamed: Q67.3 (G), Q70.3 (D), R167.2
unnamed: Q68.1 (G), Q74.3 (D), R171.1
unnamed: Q68.3 (G), Q71.3 (D), R168.2
unnamed: Q75.1 (G), Q81.3 (D), R181.1
unnamed: Q75.3 (G), Q78.3 (D), R178.2
unnamed: Q76.1 (G), Q82.3 (D), R182.1
unnamed: Q76.3 (G), Q79.3 (D), R179.2
unnamed: Q77.1 (G), Q83.3 (D), R183.1
unnamed: Q77.3 (G), Q80.3 (D), R180.2

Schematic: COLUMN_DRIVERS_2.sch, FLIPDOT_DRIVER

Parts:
Q84, Q85, Q86, Q93, Q94, Q95: DMG6602; TSOT-23-6
Q87, Q88, Q89, Q90, Q91, Q92, Q96, Q97, Q98, Q99, Q100, Q101: SSM3K35AMFV; SOT-723
R190, R191, R192, R193, R194, R195, R196, R197, R198, R199, R200, R201, R202, R203, R204, R205, R206, R207, R208, R209, R210, R211, R212, R213: CRG0603F4K7; R_0603_1608Metric; TOLERANCE 5%

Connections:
+12V: Q84.2 (S), Q85.2 (S), Q86.2 (S), Q93.2 (S), Q94.2 (S), Q95.2 (S), R190.1, R191.1, R192.1, R202.1, R203.1, R204.1; also elsewhere on the board
COL12: Q84.4 (D), Q84.6 (D); also elsewhere on the board
COL12_OFF: R193.2, R197.1; also elsewhere on the board
COL12_ON: Q87.1 (G), Q90.1 (G), R196.1; also elsewhere on the board
COL13: Q85.4 (D), Q85.6 (D); also elsewhere on the board
COL13_OFF: R194.2, R199.1; also elsewhere on the board
COL13_ON: Q88.1 (G), Q91.1 (G), R198.1; also elsewhere on the board
COL14: Q86.4 (D), Q86.6 (D); also elsewhere on the board
COL14_OFF: R195.2, R201.1; also elsewhere on the board
COL14_ON: Q89.1 (G), Q92.1 (G), R200.1; also elsewhere on the board
COL15: Q93.4 (D), Q93.6 (D); also elsewhere on the board
COL15_OFF: R205.2, R209.1; also elsewhere on the board
COL15_ON: Q96.1 (G), Q99.1 (G), R208.1; also elsewhere on the board
COL16: Q94.4 (D), Q94.6 (D); also elsewhere on the board
COL16_OFF: R206.2, R211.1; also elsewhere on the board
COL16_ON: Q97.1 (G), Q100.1 (G), R210.1; also elsewhere on the board
COL17: Q95.4 (D), Q95.6 (D); also elsewhere on the board
COL17_OFF: R207.2, R213.1; also elsewhere on the board
COL17_ON: Q98.1 (G), Q101.1 (G), R212.1; also elsewhere on the board
GND: Q84.5 (S), Q85.5 (S), Q86.5 (S), Q87.2 (S), Q88.2 (S), Q89.2 (S), Q90.2 (S), Q91.2 (S), Q92.2 (S), Q93.5 (S), Q94.5 (S), Q95.5 (S), Q96.2 (S), Q97.2 (S), Q98.2 (S), Q99.2 (S), Q100.2 (S), Q101.2 (S), R196.2, R197.2, R198.2, R199.2, R200.2, R201.2, R208.2, R209.2, R210.2, R211.2, R212.2, R213.2; also elsewhere on the board
unnamed: Q84.1 (G), Q90.3 (D), R193.1
unnamed: Q84.3 (G), Q87.3 (D), R190.2
unnamed: Q85.1 (G), Q91.3 (D), R194.1
unnamed: Q85.3 (G), Q88.3 (D), R191.2
unnamed: Q86.1 (G), Q92.3 (D), R195.1
unnamed: Q86.3 (G), Q89.3 (D), R192.2
unnamed: Q93.1 (G), Q99.3 (D), R205.1
unnamed: Q93.3 (G), Q96.3 (D), R202.2
unnamed: Q94.3 (G), Q97.3 (D), R203.2
unnamed: Q95.3 (G), Q98.3 (D), R204.2
unnamed: Q94.1 (G), Q100.3 (D), R206.1
unnamed: Q95.1 (G), Q101.3 (D), R207.1

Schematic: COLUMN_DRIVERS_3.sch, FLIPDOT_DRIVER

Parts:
Q102, Q103, Q104, Q111, Q112, Q113: DMG6602; TSOT-23-6
Q105, Q106, Q107, Q108, Q109, Q110, Q114, Q115, Q116, Q117, Q118, Q119: SSM3K35AMFV; SOT-723
R214, R215, R216, R217, R218, R219, R220, R221, R222, R223, R224, R225, R226, R227, R228, R229, R230, R231, R232, R233, R234, R235, R236, R237: CRG0603F4K7; R_0603_1608Metric; TOLERANCE 5%

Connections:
+12V: Q102.2 (S), Q103.2 (S), Q104.2 (S), Q111.2 (S), Q112.2 (S), Q113.2 (S), R214.1, R215.1, R216.1, R226.1, R227.1, R228.1; also elsewhere on the board
COL18: Q102.4 (D), Q102.6 (D); also elsewhere on the board
COL18_OFF: R217.2, R221.1; also elsewhere on the board
COL18_ON: Q105.1 (G), Q108.1 (G), R220.1; also elsewhere on the board
COL19: Q103.4 (D), Q103.6 (D); also elsewhere on the board
COL19_OFF: R218.2, R223.1; also elsewhere on the board
COL19_ON: Q106.1 (G), Q109.1 (G), R222.1; also elsewhere on the board
COL20: Q104.4 (D), Q104.6 (D); also elsewhere on the board
COL20_OFF: R219.2, R225.1; also elsewhere on the board
COL20_ON: Q107.1 (G), Q110.1 (G), R224.1; also elsewhere on the board
COL21: Q111.4 (D), Q111.6 (D); also elsewhere on the board
COL21_OFF: R229.2, R233.1; also elsewhere on the board
COL21_ON: Q114.1 (G), Q117.1 (G), R232.1; also elsewhere on the board
COL22: Q112.4 (D), Q112.6 (D); also elsewhere on the board
COL22_OFF: R230.2, R235.1; also elsewhere on the board
COL22_ON: Q115.1 (G), Q118.1 (G), R234.1; also elsewhere on the board
COL23: Q113.4 (D), Q113.6 (D); also elsewhere on the board
COL23_OFF: R231.2, R237.1; also elsewhere on the board
COL23_ON: Q116.1 (G), Q119.1 (G), R236.1; also elsewhere on the board
GND: Q102.5 (S), Q103.5 (S), Q104.5 (S), Q105.2 (S), Q106.2 (S), Q107.2 (S), Q108.2 (S), Q109.2 (S), Q110.2 (S), Q111.5 (S), Q112.5 (S), Q113.5 (S), Q114.2 (S), Q115.2 (S), Q116.2 (S), Q117.2 (S), Q118.2 (S), Q119.2 (S), R220.2, R221.2, R222.2, R223.2, R224.2, R225.2, R232.2, R233.2, R234.2, R235.2, R236.2, R237.2; also elsewhere on the board
unnamed: Q102.1 (G), Q108.3 (D), R217.1
unnamed: Q102.3 (G), Q105.3 (D), R214.2
unnamed: Q103.1 (G), Q109.3 (D), R218.1
unnamed: Q103.3 (G), Q106.3 (D), R215.2
unnamed: Q104.1 (G), Q110.3 (D), R219.1
unnamed: Q104.3 (G), Q107.3 (D), R216.2
unnamed: Q111.1 (G), Q117.3 (D), R229.1
unnamed: Q111.3 (G), Q114.3 (D), R226.2
unnamed: Q112.1 (G), Q118.3 (D), R230.1
unnamed: Q112.3 (G), Q115.3 (D), R227.2
unnamed: Q113.1 (G), Q119.3 (D), R231.1
unnamed: Q113.3 (G), Q116.3 (D), R228.2

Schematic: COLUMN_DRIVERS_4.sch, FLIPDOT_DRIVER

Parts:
Q120, Q121, Q122, Q129: DMG6602; TSOT-23-6
Q123, Q124, Q125, Q126, Q127, Q128, Q130, Q131: SSM3K35AMFV; SOT-723
R238, R239, R240, R241, R242, R243, R244, R245, R246, R247, R248, R249, R250, R251, R252, R253: CRG0603F4K7; R_0603_1608Metric; TOLERANCE 5%

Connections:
+12V: Q120.2 (S), Q121.2 (S), Q122.2 (S), Q129.2 (S), R238.1, R239.1, R240.1, R250.1; also elsewhere on the board
COL24: Q120.4 (D), Q120.6 (D); also elsewhere on the board
COL24_OFF: R241.2, R245.1; also elsewhere on the board
COL24_ON: Q123.1 (G), Q126.1 (G), R244.1; also elsewhere on the board
COL25: Q121.4 (D), Q121.6 (D); also elsewhere on the board
COL25_OFF: R242.2, R247.1; also elsewhere on the board
COL25_ON: Q124.1 (G), Q127.1 (G), R246.1; also elsewhere on the board
COL26: Q122.4 (D), Q122.6 (D); also elsewhere on the board
COL26_OFF: R243.2, R249.1; also elsewhere on the board
COL26_ON: Q125.1 (G), Q128.1 (G), R248.1; also elsewhere on the board
COL27: Q129.4 (D), Q129.6 (D); also elsewhere on the board
COL27_OFF: R251.2, R253.1; also elsewhere on the board
COL27_ON: Q130.1 (G), Q131.1 (G), R252.1; also elsewhere on the board
GND: Q120.5 (S), Q121.5 (S), Q122.5 (S), Q123.2 (S), Q124.2 (S), Q125.2 (S), Q126.2 (S), Q127.2 (S), Q128.2 (S), Q129.5 (S), Q130.2 (S), Q131.2 (S), R244.2, R245.2, R246.2, R247.2, R248.2, R249.2, R252.2, R253.2; also elsewhere on the board
unnamed: Q120.1 (G), Q126.3 (D), R241.1
unnamed: Q120.3 (G), Q123.3 (D), R238.2
unnamed: Q121.1 (G), Q127.3 (D), R242.1
unnamed: Q121.3 (G), Q124.3 (D), R239.2
unnamed: Q122.1 (G), Q128.3 (D), R243.1
unnamed: Q122.3 (G), Q125.3 (D), R240.2
unnamed: Q129.1 (G), Q131.3 (D), R251.1
unnamed: Q129.3 (G), Q130.3 (D), R250.2

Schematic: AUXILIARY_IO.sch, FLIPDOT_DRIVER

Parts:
D11, D12: LED_GENERIC_0805; D_0805_2012Metric
J3: Conn_01x03_Male; PinHeader_1x03_P2.54mm_Horizontal
J4, J5, J6: PTH_1.5_mm; TestPoint_THTPad_D3.0mm_Drill1.5mm
Q4, Q5: SSM3K35AMFV; SOT-723
R20, R26, R36: ‎RMCF0603FT470R‎; R_0603_1608Metric; TOLERANCE 1%
R28, R35, R37: CRG0603F4K7; R_0603_1608Metric; TOLERANCE 5%
SW1, SW3, SW4: TACTILE_SWITCH_SMALL
U6: NP_CM1293A-04SO; SOT-457

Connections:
+3V3: R20.1, R26.1, R36.1, SW1.2, SW3.2, SW4.2, U6.4 (CH3), U6.5 (V+); also elsewhere on the board
GND: Q4.2 (S), Q5.2 (S), R28.2, R35.2, R37.2, U6.2 (V-); also elsewhere on the board
unnamed: D11.1 (K), Q4.3 (D)
unnamed: D12.1 (K), Q5.3 (D)

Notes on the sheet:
LABEL PINS ON SILKSCREEN
SILKSCREEN: POPULATE TVS DIODES AS APPROPRIATE FOR USE WITH GPIO PERIPHERALS

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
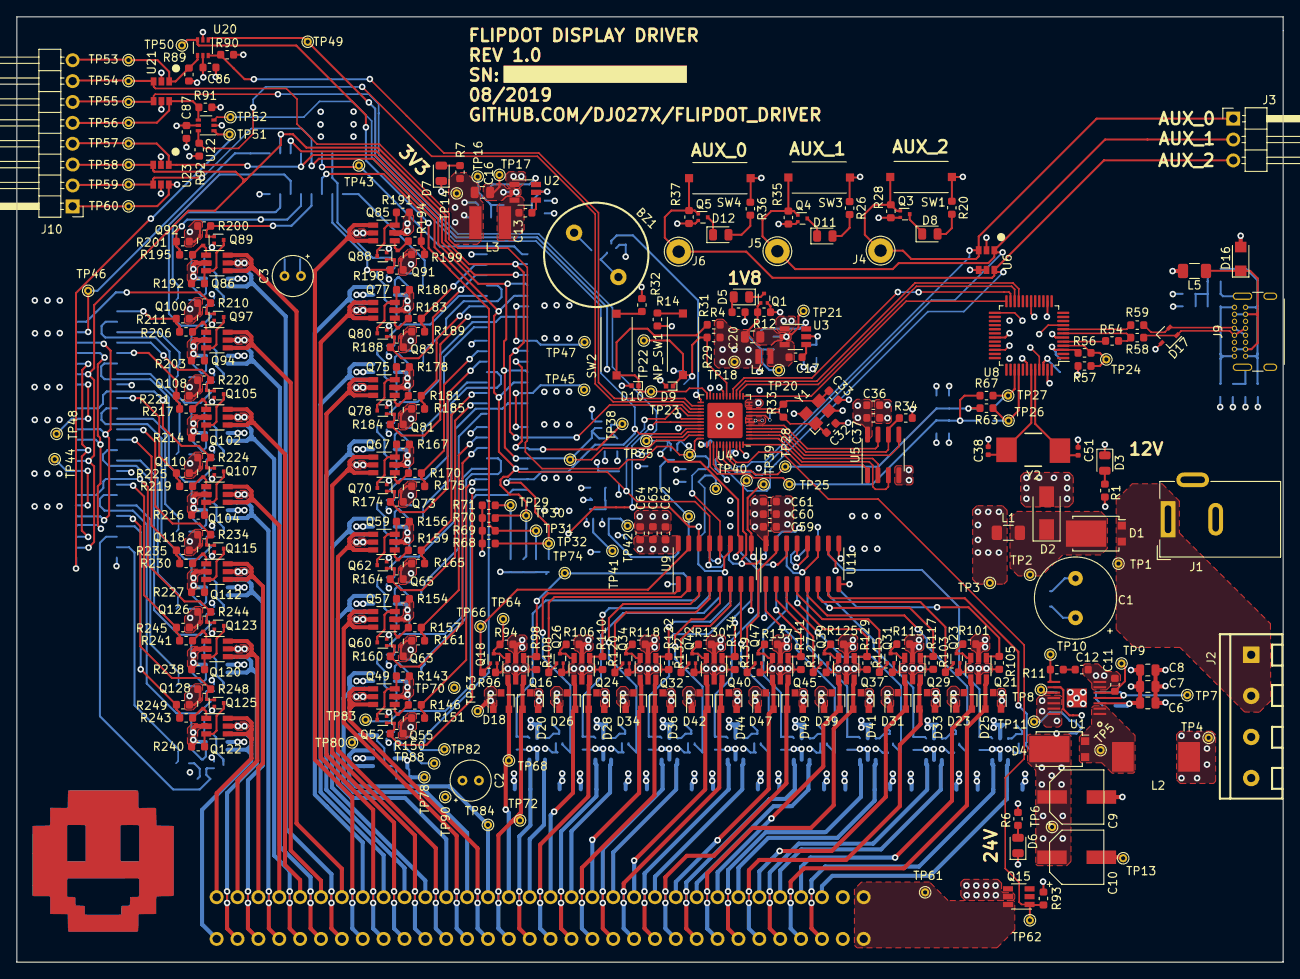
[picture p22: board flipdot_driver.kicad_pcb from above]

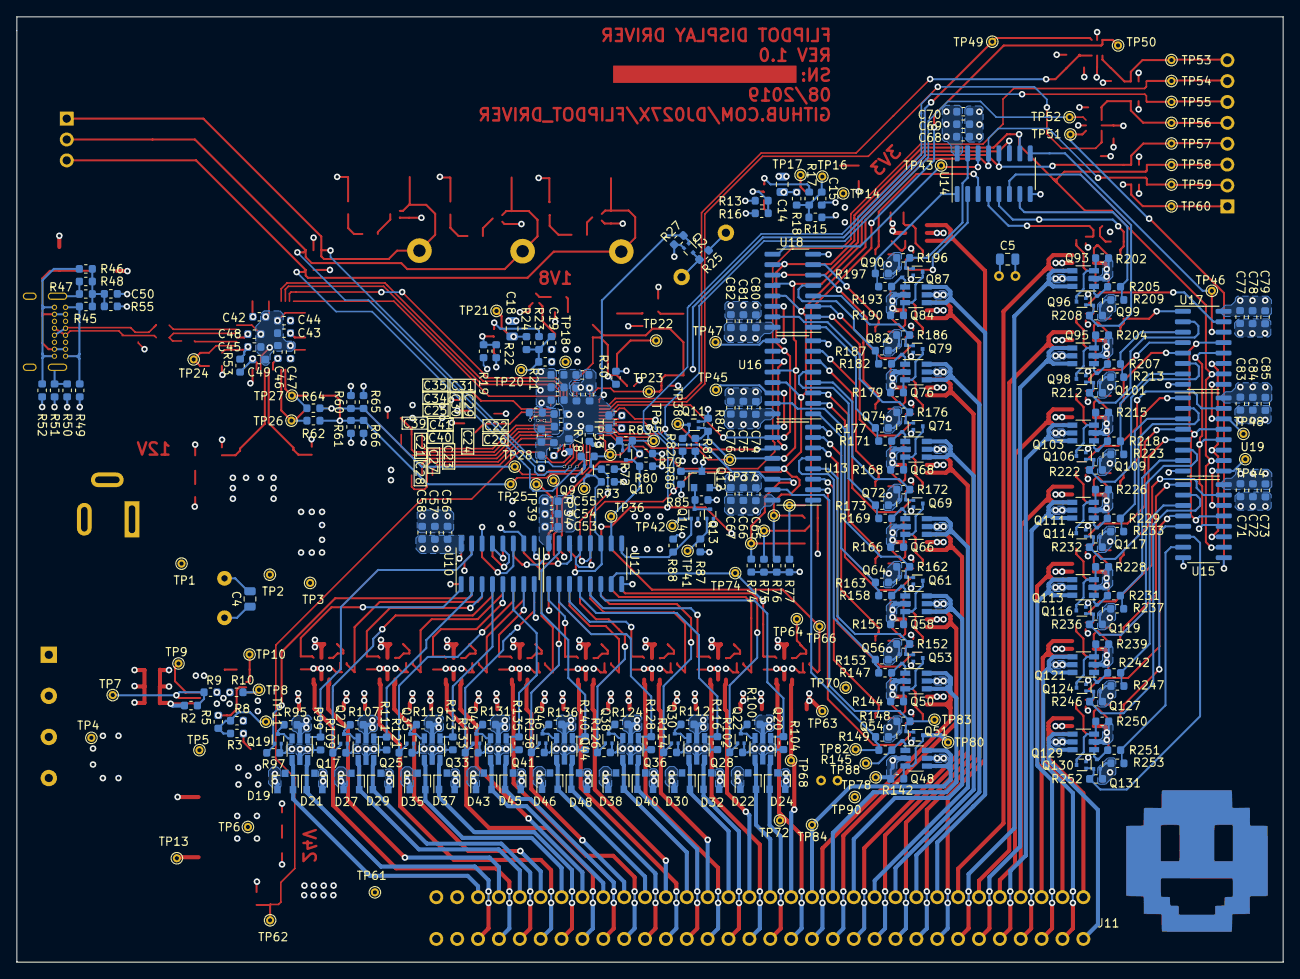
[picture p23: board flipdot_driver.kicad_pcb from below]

Board: 4 copper layers, 154.1 x 115.0 mm, 623 parts (300 on the bottom side), 327 nets.

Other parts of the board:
D8: LED_GENERIC_0805; D_0805_2012Metric
Q3: SSM3K35AMFV; SOT-723

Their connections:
GND: Q3.2; also elsewhere on the board
unnamed: D8.1, Q3.3

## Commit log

2017-12-11 replaced relatively large power MOSFETs with much more space-efficient N P pairs in a TSOT-23-6 package
    [flipdot_driver.sch]
2017-12-12 Added DC-DC converters to attain necessary voltage rails
    [BoM.ods, flipdot_driver.sch]
2017-12-12 Sprinkled in some test points on the power circuitry
    [flipdot_driver.sch]
2017-12-23 Ignore this commit; shouldn't be any changes
    [flipdot_driver.sch]
2018-01-04 STARTED WORK ON CLOCK CIRCUITS FOR FE310-G000 AND FTD2232D CHIPS. ALSO DECIDED TO OPTIMIZE DIGITAL BOARD/BOARD INTERFACE TO REDUCE CABLE COST BY ADDING OPTOISOLATORS ON THE BOARD, GETTING RID OF INVE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
    [flipdot_driver.sch]
2018-01-05 cleaned up clock circuits and created a footprint for the crystals. Still considering wheter to propgate the JTAG chain through all connected boards
    [flipdot_driver.sch]
2018-05-18 Thank goodness for version control! Accidentally deleted the signal inverters at some point, but the initial commit still had them! Added those, beefed up circuit protection with reverse input diode,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
    [flipdot_driver.sch]
2018-05-22 Changed bias resistors to more sane values and included my kicad library
    [flipdot_driver.sch]
2018-05-23 moar bugfixes
    [flipdot_driver.sch]
2018-05-23 bugfixes and added aux io
    [flipdot_driver.sch]
2018-07-01 Moved my cucstom components here, and made a bunch of changes to schematic
    [flipdot_driver.sch]
2018-07-19 Cleaned repo up some
    [BoM.ods, flipdot_driver.sch]
2018-07-25 updated whole project from kicad 4 to 5
    [flipdot_driver.sch]
2018-09-06 removed the need for 5V0 rail. Have begun building my library up with actual components, so that the schematic links to specific part numbers instead of generic symbols
2018-09-07 continued assigning caps to actual parts
    [flipdot_driver.sch]
2019-05-27 Swapped discrete TVS with arrays. Swapped LED PWM PMOS (Q89)
    [flipdot_driver.csv, flipdot_driver.sch]
2019-06-06 automated commit
    [FE310.sch, flipdot_driver.sch]
2019-06-08 Fixed page order again, annotated schamatic, and plotted a PDF
    [AUXILIARY_IO.sch, COLUMN_DRIVERS_4.sch, COLUMN_SHIFT_REGISTER.sch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]
